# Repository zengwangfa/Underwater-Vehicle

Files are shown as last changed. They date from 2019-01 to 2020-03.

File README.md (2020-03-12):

# ROV/AUV航行器控制中心

<p align="center">
  <a href="https://zengwangfa.top/">个人主页🕺|</a>
  <a href="./software/README.md">软件说明💻|</a>
  <a href="./hardware/README.md">硬件说明📚|</a>
  <a href="./graphic_model/README.md">机械说明🎮</a>
</p>

---

<p align="center">
  
  
  
  
</p>

## 1、简介

| 硬件 | 主控制器(STM32) | 视频与数据服务器(树莓派3B+) | 
| :--: | :--: | :--: |
|芯片型号| [STM32F407ZGT6](/docs/DataSheet/STM32F407ZGT6.pdf) | [BCM2837B0](/docs/DataSheet/BCM2835-ARM-Peripherals.pdf) |
|CPU| 32位 Cortex-M4(ARMv7) | 64位 Cortex-A53(ARMv8) |
|主频| 168MHz | 1.4GHz |
|RAM| 192KB | 1GB |
|外存| 1MB(FLASH) | 32GB(SD) |
|单元| FPU、DSP | 千兆以太网 |
|操作系统| [RT-Thread](https://www.rt-thread.org/) | [Liunx](https://www.linux.org/) |
- 系统结构简图：
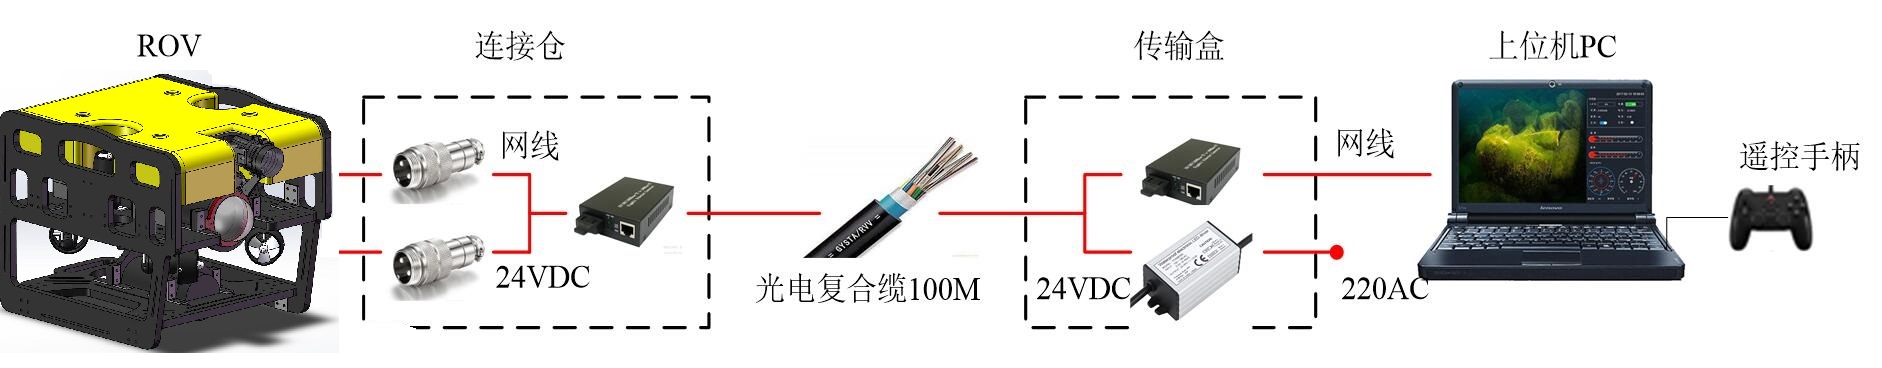
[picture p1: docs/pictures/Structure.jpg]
系统结构简图


## 2、目录说明
```
+——Underwater_vehicle
|---- docs: 【设计文档】
|---- hardware:【电路设计】      
|---+ software:【软件设计】
|       ├──README.md
|       ├──rt-thread-master
|            └──bsp
|               └──stm32f407【控制程序】
|---- graphic_model:【机械模型】
|---- raspberry_server:【树莓派服务】
|---- tools:【调试工具】
|---- README.md
```

## 3、机械结构
- 3维模型
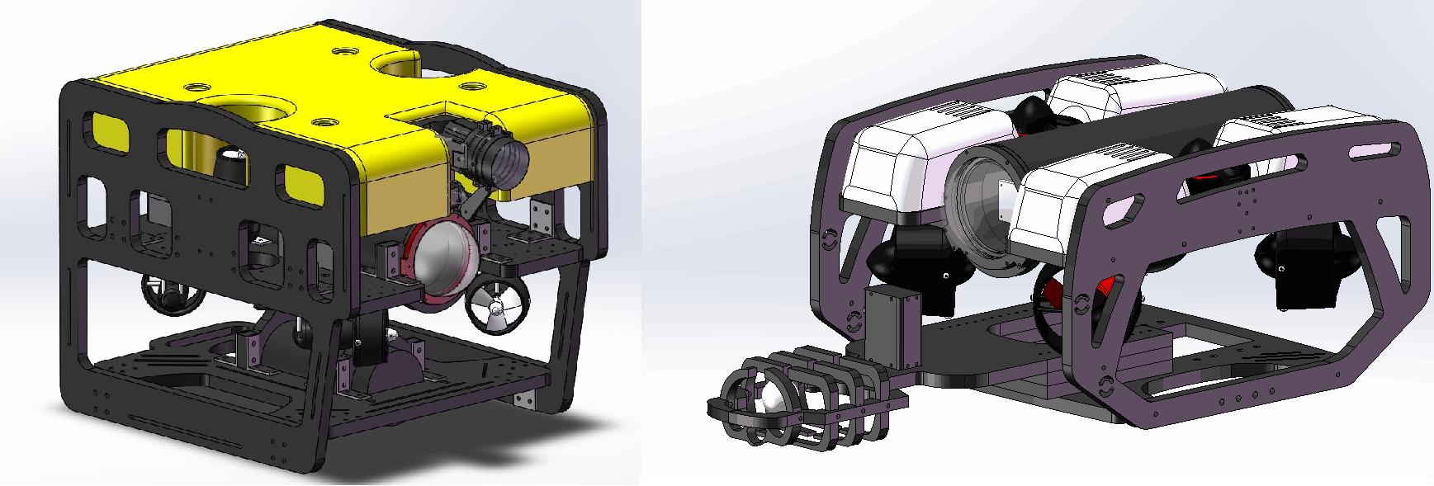
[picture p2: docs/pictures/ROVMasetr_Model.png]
ROV 3D ROVMaser Model


- 实物图
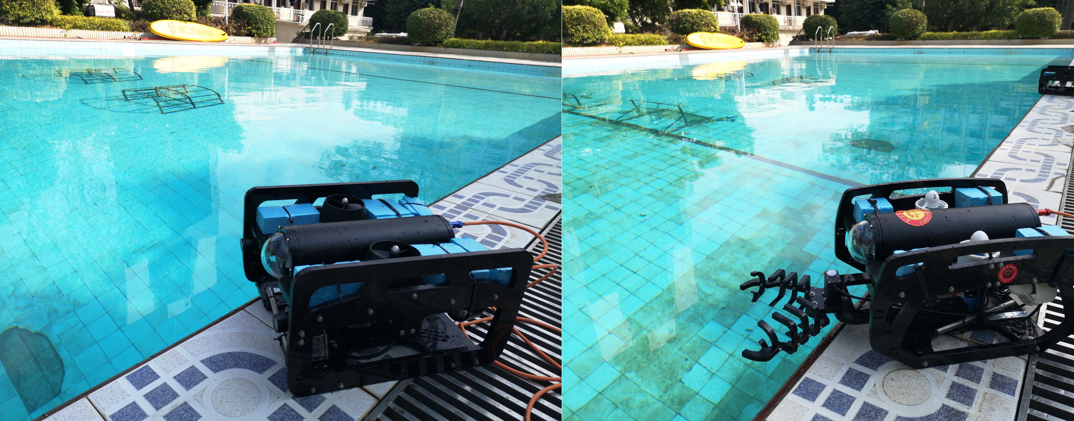
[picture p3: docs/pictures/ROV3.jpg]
Entity ROV Entity


## 4、软件结构
Connect Flow

- Computer Connect
- Raspberry Pi    
- MCU Controller  

## 5、硬件结构
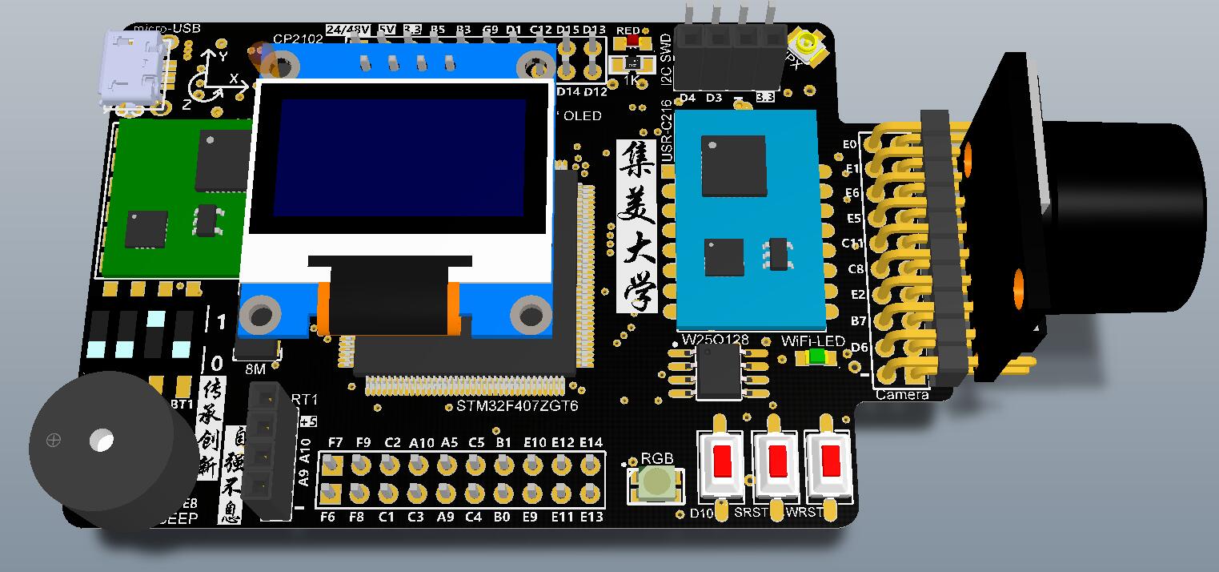
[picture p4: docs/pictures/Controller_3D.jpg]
Controller PCB 3D Controller 3D


- 核心板(Core Controller)拥有外设：

| 外设名称 | RGB LED | Key | Buzzer | Dial Switch | MS5837 | OLED | W25Q128 | Voltage Detection | Current Detection | Zigbee |  JY901 | USR-C216 | CP2102 | OV2640 Camera | Servo Motor | Searchlights | Perpellers |
| :---: | :---: | :---: | :---: | :---: | :---: | :---: | :---: | :---: | :---: | :---: | :---: | :---: | :---: | :---: | :---: | :---: | :---: |
| 控制(通讯)方式 | GPIO | GPIO | GPIO | GPIO | I2C | SPI | SPI | ADC | ADC | USART | USART | USART  | USART | DCMI-DMA | PWM | PWM | PWM |
| 功能描述 | 指示灯 | 按键 | 蜂鸣器 | 拨码开关 | 深度传感器 | 显示屏 | 闪存芯片 | 电压检测 | 电流检测 | 2.4G无线通信 | 九轴 | WiFi模块 | 串口转USB | 摄像头 | 舵机  | 探照灯 | ESC |

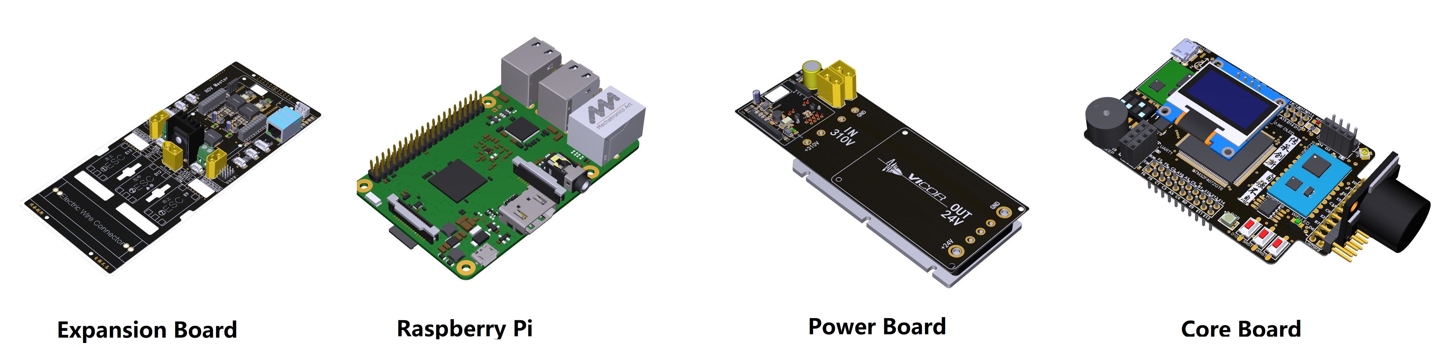
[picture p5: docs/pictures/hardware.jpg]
Hardware PCB 3D


---

- 树莓派拥有有外设：

| 外设名称 | Camera 1 | Camera 2 | Core Controller | PLC / Optical-to-electrical Transducer |
| :---: | :---: | :---: | :---: | :---: |
| 控制(通讯)方式 | USB | USB | USB | Ethernet |
| 功能描述 | 外置光学变焦摄像头 | 内置云台摄像头 | 核心控制器 | 电力载波模块/光电转换器 | 

## 6、Underwater Vehicle 的进展
- [X] 电路设计
    - [X] Core Controller核心控制板 by [@Ian](https://github.com/zengwangfa)	
	- [X] Underwater_Vehicle主板 by [@Ian](https://github.com/zengwangfa)	
	- [X] 电源主板设计 by [@Ian](https://github.com/zengwangfa)
	
- [X] 控制程序
    - [X] 外设驱动 by [@Ian](https://github.com/zengwangfa)
	- [X] 控制简易框架 by [@Ian](https://github.com/zengwangfa)
	- [X] 通信控制 by [@Ian](https://github.com/zengwangfa)
	- [X] 定向控制算法 by [@Okurarisona](https://github.com/Okurarisona) 🆕
- [X] 上位机
	- [X] C#上位机 by [@陈信任] 🆕

- [X] 机械结构
	- [X] 框架式结构CAD设计 by [@JackyLin](https://github.com/JackyLin1205) 🆕
	- [X] 电子仓、电源仓设计 by [@JackyLin](https://github.com/JackyLin1205)

- [X] 树莓派
	- [X] 数据Server服务器 by [@FatihBo](https://github.com/FatihBo)

## 7、使用说明

- propeller_power_set [parameter]
> 设置推进器动力 <0~300%>
- set_depth_sensor_type [parameter]
> 修改深度传感器 类型<ms5737/spl1301/null>
...
#### 参与贡献

- Fork 本仓库
- 新建 Feat_xxx 分支
- 提交代码
- 新建 Pull Request
- [点击联系我](Mailto:zengwangfa@outlook.com)

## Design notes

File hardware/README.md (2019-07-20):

[软件说明](./../software/README.md)|
[硬件说明](./../hardware/README.md)| 
[机械结构说明](./graphic_model/README.md)

# 1.航行器控制中心

| 硬件 | 描述 |
| -- | -- |
|芯片型号| STM32F407ZGT6 |
|CPU| Cortex-M4 |
|主频| 84MHz-168MHz |
|FLASH| 1MB |
|SRAM| 192KB |
|单元| FPU、DSP |

Controller PCB 3D Controller 3D.jpg

# 2.硬件目录
**Hardware:【相关硬件设计】**

| 目录组 | 描述 |
| --- | --- |
| Core Controller | ROV核心控制板PCB文件 |
| Depth Sensor | 深度传感器MS5837 V1.0 |
| Robot Main Board | ROV主控板PCB文件及Robot设备管理文件 |
| SMT | 钢网PDF文件 |
| Zoom Camrea Controller | 变焦摄像头PCB文件 |
# 3.硬件架构

- 拥有外设：

| 外设名称 | RGB LED | Key | Buzzer | Dial Switch | MS5837 | OLED | W25Q128 | Voltage Detection | Current Detection | Zigbee |  JY901 | USR-C216 | CP2102 | OV2640 Camera | Servo Motor | Searchlights | Perpellers |
| --- | --- | --- | --- | --- | --- | --- | --- | --- | --- | --- | --- | --- |  --- | --- |  --- |  --- | --- |
| 控制方式 | GPIO | GPIO | GPIO | GPIO | I2C | SPI | SPI | ADC | ADC | USART | USART | USART  | USART | DCMI-DMA | PWM | PWM | PWM |
| 功能描述 | 指示灯 | 按键 | 蜂鸣器 | 拨码开关 | 深度传感器 | 显示屏 | 闪存芯片 | 电压检测 | 电流检测 | 2.4G无线通信 | 九轴 | WiFi模块 | 串口转USB | 摄像头 | 舵机  | 探照灯 | 推进器 |

- 指示灯：显示系统工作状态[绿色闪烁为正常、红色常亮为异常]
- 按键：目前为切换OLED界面
- 蜂鸣器：报警提示作用
- 拨码开关：切换状态
- 深度传感器：采集水压、水温,并转换为深度值
- OLED显示屏：显示相关数据及状态
- 闪存芯片：存储相关变量及参数
- 电压检测：检测电源电压
- 电流检测：检测总电流大小,用于过流保护
- 2.4G通信模块：用于与操作系统交互
- 九轴：采集加速度、角速度、磁场、角度[偏航角Yaw、横滚角Roll、俯仰角Pitch]
- WiFi模块：用于上位机数据示波器显示及调参
- 串口转USB：用于与**树莓派**通信
- 摄像头：STM32自带摄像头,可用于扩展
- 舵机：分为云台舵机、机械手舵机
- 探照灯：用于水下照明
- 推进器：ROV/AUV动力来源

```
+——Underwater_vehicle
|--------+──DC 24V/48V 【Power management】 
|--------+──STM32F407ZGT6 【Control-Center】                  
|        |       └──【Normal Peripherals】
|        │       ├── RGB [GPIO]   
|        │       ├── KEY [GPIO] 
|        │       ├── BUZZER [GPIO]      
|        │       ├── Dial Switch [GPIO]   
|        │       ├── OLED [Software SPI]       
|        │       ├── Voltage Detection [ADC]             
|        │       ├── Bluetooth [UART]       
|        │       ├── W25Q128 FLASH [SPI]
|        │       ├── USB to serial port CP2102 UART Bridge [UART]
|        │       └──......  
|        |       └── 【Important Peripherals】
|        |       ├── Nine axis gyroscope [UART]
|        |       ├── USR-C216 Wifi [UART]   
|        |       ├── OV2640 Camera [DCMI-DMA]
|        |       └──...... 
|        +──Vehicle Devices
|        └── Searchlights [GPIO]
|        ├── Propellers [PWM]
|        ├── Servo Motor for Mechanical Arm [PWM]
|        ├── CAMERAs 
|        └──...... 
```
输入图片说明
输入图片说明 Controller PCB.jpg
------
### 2.1 电源及 USB
核心板可以通过 Micro-USB 或 5V 电源供电。使用 Micro-USB 接到电脑时，电脑弹出串口CP210x USB to UART Bridge。连接该串口后，可以通过 shell 命令行工具进行交互，也可以查看实时的日志信息。

### 2.2 功能接口
|接口|数量|备注|
|:-:|:-:|:-:|
|GPIO|2路|其他路均可复用为GPIO|
|DAC|1路|DAC2|
|ADC|5路|ADC123|
|TIM|16路|TIM4等|
|UART|2路|UART4 —— UART5|
|SPI|1路|SPI1|
|CAN|1路|CAN1|
|OV-Camera|1路|DCMI|

### 2.3 其他接口

|接口|数量|备注|
|:-:|:-:|:-:|
|POWER IN|1路|电源电压接入口|
|Bluetooth|1路|UART4|
|SWD调试接口|1路|SWD|
|气压计|1路|I2C|
|OLED|1路| SPI|
|BOOT|1路|BOOT0|
|GND|2路|电源地接入口|
|+5V|1路|+5V电压接入口|
|+3.3V|1路|+3.3V电压接入口|

### 2.4 指示灯
- Power-LED:+3.3V电源指示灯
- RGB: User 自定义指示灯
- Wifi-LED: Wifi连接指示灯

### 2.5 按键
- WRST:Wifi RESET 恢复出厂设置按键【长按3s】
- SRST:STM32 RESET 复位
- D10:GPIO-PD10 自定义【OLED下一页】

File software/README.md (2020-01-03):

[软件说明](./../software/README.md) |
[硬件说明](./../hardware/README.md) | 
[机械结构说明](./graphic_model/README.md)



- 本项目用用到了两个实用的软件包：
	- [EasyFlash](https://github.com/armink/EasyFlash)一款开源的轻量级嵌入式Flash存储器库
	- [EasyLogger](https://github.com/armink/EasyLogger)一款超轻量级、高性能的 C/C++ 日志库

# 1.目录说明

**software:【相关软件设计】**
```c
   └──Camera 【OV2640例程】
   ├──RT-Thread 【RTT示例】
   ├──rt-thread-master
        └──bsp
            └──stm32f40x 【控制中心程序】

```			

| 目录组 | 描述 |
| -- | -- |
|Kernel| 它用于存放RT-Thread内核源文件 |
|User| 它用于存放用户应用文件 |
|Applications| 它用于存放外设应用程序 |
|Drivers|  它用于存放相关外设驱动 |
|STM32_StdPeriph| 它用于存放STM32固件库文件 |
|cpu|  它用于存放内核相关文件 |
|Fliesystem| 它用于存放虚拟文件系统 |
|DeviceDrivers|  它用于存放RT-Thread驱动 |
|finsh| 它用于存放RT-Thread Finsh组件 |
|libc| 它用于存放RT-Thread 相关文件 |
|Easylogger| 它用于存放RT-Thread Easylogger组件 |
|EasyFlash| 它用于存放RT-Thread EasyFlash |
|Utilities| 它用于存放相关工具与滤波算法 |

# 2.软件结构
```
+——RT-Thread
|    └──Kernel 【RT-Thread内核初始化】                  
|    ├── Normal Peripherals Init 【普通外设初始化】
|    ├── System self-check 【系统自检:检测是否所有外设初始化完成】 
|           └── Read Gyroscope data 【读取JY901 九轴数据】 
|           ├── Detection input devices 【检测输入设别】 
|           ├── Attitude Control 【姿态控制】 	
|    └──...... 
```

# 3.定义通信协议

## 3.1 PC端发送的控制数据包

- 全部数据按照**16进制**
- 定义机头方向为X轴,机头朝向为x正方向
- 定义垂直于机头方向为y轴,向左为y正方向

| 编号 | 1 | 2 | 3 | 4 | 5 | 6 | 7 | 8 | 9 | 10 | 11 | 12 | 13 | 14 | 15  | 16 | 17 | 18 | 19 | 20 | 
| --- | --- | --- | --- | --- | --- | --- | --- | --- | --- | --- | --- | --- | --- | --- | --- | --- | --- | --- | --- | --- |
| 数据所代表的含义 | 包头 | 包头 | 数据长度位 | 深度锁定位 | 方向锁定位 | X轴动力模拟量 | Y轴动力模拟量 | 垂直运动方向位 | 旋转运动方向位 | 油门量 | 灯亮度控制位 | 变焦摄像头动作位 | 云台控制位 | 机械臂控制位 | Reserve | Reserve | Reserve | Reserve | 启动停止位 | 校验位 |  
| 具体描述 | AA | 55 | 10 |  |  |  |  |  |  |  |  |  |  |  | x | x | x | x | ON/OFF | SUM | 
| 数组编号 | 0 | 1 | 2 | 3 | 4 | 5 | 6 | 7 | 8 | 9 | 10 | 11 | 12 | 13 | 14 | 15  | 16 | 17 | 18 | 19 | 

控制字格式：0xAA 0x55 0x10+控制字节(16字节)+校验字(所有字节相加后，保留最后一个字节)

- 第1字节：包头位
- 第2字节：包头位
- 第3字节：数据长度位
- 第4字节：0x01表示深度锁定，0x02表示人工控制（可指定默认值）
- 第5字节：0x01表示方向锁定，0x02表示随水动（可指定默认值）
- 第6字节：【左摇杆上下状态】摇杆模拟量 前后状态（0~255）即摇杆居中时为128（即停止），最下为0，最上位255 
- 第7字节：【左摇杆左右状态】摇杆模拟量 左右状态（0~255）即摇杆居中时为128（即停止），最左为0，最右为255
- 第8字节：【右摇杆上下状态】摇杆模拟量 上下状态（0~255）即摇杆居中时为128（即停止），最下为0，最上位255 
- 第9字节：【右摇杆左右状态】摇杆模拟量 旋转状态（0~255）即摇杆居中时为128（即停止止），最左为0，最右为255
- 第10字节：0x00~0xff (0~255) 表示的油门大小：4档位可调，LB加档，LT减档，可分别设置4个档位油门大小 【不用】
- 第11字节：灯的亮度控制，0x01表示变亮，0x02表示变暗，0x00表示不动作（默认）
- 第12字节：摄像头焦距控制，0x01表示聚焦，0x02表示变放焦， 0x11表示放大，0x12表示缩小，0x00表示不动作（默认）
- 第13字节：云台转动，0x01表示向上，0x02表示向下，0x03表示归中，0x00表示不动作（默认）
- 第14字节：机械手动作，0x01表示张开，0x02表示关闭，0x00表示不动作（默认）
- 第15字节：保留(reserve)
- 第16字节：保留(reserve)
- 第17字节：保留(reserve)
- 第18字节：保留(reserve)
- 第19字节：0x00 默认 0x01表示启动， 0x02表示停止
- 第20字节：累加和校验

## 3.2 ROV/AUV返回的数据包

控制字格式：0xAA 0x55 0x16+控制字节(22字节) +校验字(所有字节相加后，保留最后一个字节)

- 第一，二字节：电压第一字节表示整数部分，第二字节小数部分
- 第三，四字节：舱外水温度第一字节表示整数部分，第二字节小数部分
- 第五，六字节：舱内CPU内核温度第一字节表示整数部分，第二字节小数部分
- 第七字节：深度值（0~16777215cm）精确到厘米 【高8位】
- 第八字节：深度值（0~16777215cm）精确到厘米 【中8位】
- 第九字节：深度值（0~16777215cm）精确到厘米 【低8位】
##### 深度值共由3个字节，24位组成
- 第十字节：航向角（Yaw）  【高8位】记为YawH
- 第十一字节：航向角（Yaw）【低8位】记为YawL
计算方法：偏航角（z 轴）Yaw=((YawH<<8)|YawL)/32768*180(°)
航向角（Yaw），两字节(0~359)可用0度代表正北方，90度代表正东，以此类推

- 第十二字节：俯仰角（Pitch）【高8位】记为PitchH
- 第十三字节：俯仰角（Pitch）【低8位】记为PitchL
计算方法：俯仰角（y 轴）Pitch =((PitchH<<8)| PitchL)/32768*180(°)
俯仰角（Pitch），可用0°表示水平

- 第十四字节：横滚角（Roll）【高8位】记为RollH
- 第十五字节：横滚角（Roll）【低8位】记为RollL
计算方法：横滚角（x 轴）Roll =((RollH<<8)| RollL)/32768*180(°)
横滚角（Roll），可用0°表示水平

- 第十六字节：航行速度（0~255）单位m/s

- 第17字节：设备状态标志，0x00表示都正常操作，0x01表示机械手开到头了，0x02表示摄像头转到头了，0x03表示机械手和摄像头都转到头了

| 设备状态标志8bit | 1 | 1 | 1 | 1 | 1 | 1 | 1 | 1 |
| :---: | :---: |  :---: |  :---: | :---: |  :---: | :---: | :---: | :---: |
| 代表含义 |深度传感器初始化成功  | 所有串口设备初始化成功 | IO设备初始化成功 |PWM设备初始化成功  | 聚焦开到头 | 变焦开到头 | 云台开到头 |机械手到头  |

- 第18字节：本设备的启动停止位（若返回的为0x01，代表本设备为启动状态；若为0x02 或 0x00，代表本设备为停止状态；则上位机 【P】图标需要对应）
- 第19字节：保留
- 第20字节：保留
- 第21字节：保留
- 第22字节：保留

所以，我们发送的字符串就应该为：
0xAA 0x55 0x10 控制字节(16字节) 校验字(所有字节相加后，保留最后一个字节)
若需其他的数据发送，按照此数据格式自行添加即可

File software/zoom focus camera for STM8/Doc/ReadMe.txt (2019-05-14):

一、工程说明
    1、时间：    2017年06月29日
    2、开发环境：IAR for STM8 V2.20
    3、标准库：  V2.2.0
    4、工程版本：V1.0.0
    5、目标芯片：STM8S/AF系列芯片

二、提示：
    本工程适合STM8S和STM8AF系列芯片，包含：
    STM8S208、STM8S207、STM8S007、STM8AF52Ax、STM8AF62Ax、STM8S105、
    STM8S005、STM8AF626x、STM8AF622x、STM8S103、STM8S003、STM8S903

    只要没有特别说明，工程都适合以上芯片，只需要修改配置为对应芯片即可。
    修改两个地方：
    1.Device芯片型号：Project -> Options -> General Options -> Target -> Device
    2.芯片型号预定义：Project -> Options -> C/C++ Compiler -> Preprocessor -> Defined Symbols

三、帮助
    微信搜索公众号：EmbeddDeveloper, 关注, 查看更多精彩内容。

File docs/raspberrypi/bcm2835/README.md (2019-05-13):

# BCM2835

The Broadcom chip used in the Raspberry Pi Model A, B, B+, Compute Module and Raspberry Pi Zero

Please refer to:

- [Peripheral specification](BCM2835-ARM-Peripherals.pdf)
- [GPU documentation and open source driver](http://www.broadcom.com/support/)
- [ARM1176 Processor](http://www.arm.com/products/processors/classic/arm11/arm1176.php)
- [ARM1176JZF-S](http://infocenter.arm.com/help/index.jsp?topic=/com.arm.doc.ddi0301h/index.html)

Also see the Raspberry Pi 2's chip [BCM2836](../bcm2836/README.md)

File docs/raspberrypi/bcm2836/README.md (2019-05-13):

# BCM2836

The Broadcom chip used in the Raspberry Pi 2 Model B

The underlying architecture in BCM2836 is identical to BCM2835. The only significant difference is the removal of the ARM1176JZF-S processor and replacement with a quad-core Cortex-A7 cluster.

Please refer to:

- [BCM2836 ARM-local peripherals](QA7_rev3.4.pdf)
- [Cortex-A7 MPcore Processor Reference Manual](http://infocenter.arm.com/help/index.jsp?topic=/com.arm.doc.ddi0464f/index.html)

Also see the Raspberry Pi 1's chip [BCM2835](../bcm2835/README.md)

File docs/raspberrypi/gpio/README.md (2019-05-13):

# GPIO

General Purpose Input/Output pins on the Raspberry Pi

## Overview

This page expands on the technical features of the GPIO pins available on BCM2835 in general. For usage examples, see the [GPIO Usage](../../../usage/gpio/README.md) section. When reading this page, reference should be made to the BCM2835 ARM Peripherals [Datasheet](../bcm2835/README.md), section 6.

GPIO pins can be configured as either general-purpose input, general-purpose output or as one of up to 6 special alternate settings, the functions of which are pin-dependant.

There are 3 GPIO banks on BCM2835.

Each of the 3 banks has its own VDD input pin. On Raspberry Pi, all GPIO banks are supplied from 3.3V. **Connection of a GPIO to a voltage higher than 3.3V will likely destroy the GPIO block within the SoC.**

A selection of pins from Bank 0 is available on the P1 header on Raspberry Pi.

## GPIO Pads

The GPIO connections on the BCM2835 package are sometimes referred to in the peripherals datasheet as "pads" - a semiconductor design term meaning "chip connection to outside world".

The pads are configurable CMOS push-pull output drivers/input buffers. Register-based control settings are available for

- Internal pull-up / pull-down enable/disable
- Output [drive strength](http://www.scribd.com/doc/101830961/GPIO-Pads-Control2)
- Input Schmitt-trigger filtering

### Power-On States

All GPIOs revert to general-purpose inputs on power-on reset. The default pull states are also applied, which are detailed in the alternate function table in the ARM peripherals datasheet. Most GPIOs have a default pull applied.

## Interrupts

Each GPIO pin, when configured as a general-purpose input, can be configured as an interrupt source to the ARM. Several interrupt generation sources are configurable:

- Level-sensitive (high/low)
- Rising/falling edge
- Asynchronous rising/falling edge

Level interrupts maintain the interrupt status until the level has been cleared by system software (e.g. by servicing the attached peripheral generating the interrupt).

The normal rising/falling edge detection has a small amount of synchronisation built into the detection. At the system clock frequency, the pin is sampled with the criteria for generation of an interrupt being a stable transition within a 3-cycle window, i.e. a record of "1 0 0" or "0 1 1". Asynchronous detection bypasses this synchronisation to enable the detection of very narrow events.

## Alternative Functions

Almost all of the GPIO pins have alternative functions. Peripheral blocks internal to BCM2835 can be selected to appear on one or more of a set of GPIO pins, for example the I2C busses can be configured to at least 3 separate locations. Pad control, such as drive strength or Schmitt filtering, still applies when the pin is configured as an alternate function.

For more detailed information see the [Low level peripherals](http://elinux.org/RPi_Low-level_peripherals) page on the elinux wiki

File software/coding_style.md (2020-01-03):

# RT-Thread 编程风格

这是一份 RT-Thread 开发人员的开发指引。RT-Thread 做为一份开源软件，它需要由不同
的人采用合作的方式完成，这份文档是开发人员的一个指引。RT-Thread 的开发人员请遵
守这样的编程风格。同时对于使用 RT-Thread 的用户，也可通过这份文档了解 RT-Thread
代码内部一些约定从而比较容易的把握到 RT-Thread 的实现方式。

## 1.目录名称

目录名称如果无特殊的需求，请使用全小写的形式；目录名称应能够反应部分的意思，例
如各芯片移植由其芯片名称构成或芯片类别构成；components 目录下能够反映组件的意义。

## 2.文件名称

文件名称如果无特殊的需求(如果是引用其他地方，可以保留相应的名称)，请使用全小写
的形式。另外为了避免文件名重名的问题，一些地方请尽量不要使用通用化、使用频率高
的名称。

## 3.头文件定义

C语言头文件为了避免多次重复包含，需要定义一个符号。这个符号的定义形式请采用如下
的风格：

```c
    #ifndef __FILE_H__
    #define __FILE_H__
    /* header file content */
    #endif
```

即定义的符号两侧采用 "__" 以避免重名，另外也可以根据文件名中是否包含多个词语而
采用 "_" 连接起来。

## 4.文件头注释

在每个源文件文件头上，应该包括相应的版权信息，Change Log 记录：

```c
    /*
     * File      : rtthread.h
     * This file is part of RT-Thread RTOS
     * COPYRIGHT (C) 2006 - 2012, RT-Thread Development Team
     *
     *  This program is free software; you can redistribute it and/or modify
     *  it under the terms of the GNU General Public License as published by
     *  the Free Software Foundation; either version 2 of the License, or
     *  (at your option) any later version.
     *
     *  This program is distributed in the hope that it will be useful,
     *  but WITHOUT ANY WARRANTY; without even the implied warranty of
     *  MERCHANTABILITY or FITNESS FOR A PARTICULAR PURPOSE.  See the
     *  GNU General Public License for more details.
     *
     *  You should have received a copy of the GNU General Public License along
     *  with this program; if not, write to the Free Software Foundation, Inc.,
     *  51 Franklin Street, Fifth Floor, Boston, MA 02110-1301 USA.
     *
     * Change Logs:
     * Date           Author       Notes
     * 2006-03-18     Bernard      the first version
     * 2006-04-26     Bernard      add semaphore APIs
     * ...
     */
```

例如采用如上的形式。

## 5.结构体定义

结构体名称请使用小写英文名的形式，单词与单词之间采用 "_" 连接，例如：

```c
    struct rt_list_node
    {
        struct rt_list_node *next;
        struct rt_list_node *prev;
    };
```

其中，"{"，"}" 独立占用一行，后面的成员定义使用缩进的方式定义。

结构体等的类型定义请以结构体名称加上 "_t" 的形式作为名称，例如：

```c
    typedef struct rt_list_node rt_list_t;
```

因为内核中对象引用方便的缘故，采用了对象内核指针作为类型定义的形式，例如：

```c
    typedef struct rt_timer* rt_timer_t;
```

## 6.宏定义

在RT-Thread中，请使用大写英文名称作为宏定义，单词之间使用 "_" 连接，例如：

```c
    #define RT_TRUE                         1
```

## 7.函数名称、声明

函数名称请使用小写英文的形式，单词之间使用 "_" 连接。提供给上层应用使用的 API
接口，必须在相应的头文件中声明；如果函数入口参数是空，必须使用 void 作为入口参
数，例如：

```c
    rt_thread_t rt_thread_self(void);
```

## 8.注释编写

请使用英文做为注释，使用中文注释将意味着在编写代码时需要来回不停的切换中英文输
入法从而打断编写代码的思路。并且使用英文注释也能够比较好的与中国以外的技术者进
行交流。

源代码的注释不应该过多，更多的说明应该是代码做了什么，仅当个别关键点才需要一些
相应提示性的注释以解释一段复杂的算法它是如何工作的。对语句的注释只能写在它的上
方或右方，其他位置都是非法的。

## 9.缩进及分行

缩进请采用 4 个空格的方式。如果没有什么特殊意义，请在 "{" 后进行分行，并在下一
行都采用缩进的方式，例如：

```c
    if (condition)
    {
        /* others */
    }
```

唯一的例外是 swtich 语句，switch-case 语句采用 case 语句与 swtich 对齐的方式，
例如：

```c
    switch (value)
    {
    case value1:
        break;
    }
```

case 语句与前面的 switch 语句对齐，后续的语句则采用缩进的方式。

分行上，如果没有什么特殊考虑，请**不要在代码中连续使用两个以上的空行**。

## 10.大括号与空格

从代码阅读角度，建议每个大括号单独占用一行，而不是跟在语句的后面，例如：

```c
    if (condition)
    {
        /* others */
    }
```

匹配的大括号单独占用一行，代码阅读起来就会有相应的层次而不会容易出现混淆的情况。

空格建议在非函数方式的括号调用前留一个空格以和前面的进行区分，例如：

```c
    if (x <= y)
    {
        /* others */
    }

    for (index = 0; index < MAX_NUMBER; index ++)
    {
        /* others */
    }
```

建议在括号前留出一个空格(涉及的包括 if、for、while、swtich 语句)，而运算表达式
中，运算符与字符串间留一个空格。另外，不要在括号的表达式两侧留空格，例如：

```c
    if ( x <= y )
    {
        /* other */
    }
```

这样括号内两侧的空格是不允许的。

## 11.trace、log信息

在 RT-Thread 中，普遍使用的 log 方式是 rt_kprintf。rt_kprintf 在 RT-Thread 被实
现成一个采用轮询、非中断方式的字串输出，能够适合于在中断这类"即时"显示日志的场
合。因为这种轮询方式的存在，也必然会影响到日志输出的时序关系。

建议在代码中不要频繁的使用 rt_kprintf 作为日志输出，除非你真正的明白，你的代码
运行占用的时间多一些也没什么关系。

日志输出应该被设计成正常情况下是关闭状态(例如通过一个变量或宏就能够开启)，并且
当真正输出日志时，日志是易懂易定位问题的方式。"天书式"的日志系统是糟糕的，不合
理的。

## 12.函数

在内核编程中，函数应该尽量精简，仅完成相对独立的简单功能。函数的实现不应该太长
，函数实现太长，应该反思能够如何修改(或拆分)使得函数更为精简、易懂。

## 13.对象

RT-Thread 内核采用了 C 语言对象化技术，命名表现形式是：对象名结构体表示类定义、
对象名 + 动词短语形式表示类方法，例如：

```c
    struct rt_timer
    {
        struct rt_object parent;
        /* other fields */
    };
    typedef struct rt_timer* rt_timer_t;
```

结构体定义 rt_timer 代表了 timer 对象的类定义；

```c
    rt_timer_t rt_timer_create(const char* name,
        void (*timeout)(void* parameter), void* parameter,
        rt_tick_t time, rt_uint8_t flag);
    rt_err_t rt_timer_delete(rt_timer_t timer);
    rt_err_t rt_timer_start(rt_timer_t timer);
    rt_err_t rt_timer_stop(rt_timer_t timer);
```

rt_timer + 动词短语的形式表示能够应用于 timer 对象的方法。

在创建一个新的对象时，应该思考好，对象的内存操作处理：是否允许一个静态对象存在
，或仅仅支持从堆中动态分配的对象。

## 14. 用 astyle 自动格式化代码

    参数：--style=allman
          --indent=spaces=4
          --indent-preproc-block
          --pad-oper
          --pad-header
          --unpad-paren
          --suffix=none
          --align-pointer=name
          --lineend=linux
          --convert-tabs
          --verbose

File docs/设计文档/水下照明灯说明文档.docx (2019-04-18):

水下照明灯说明文档

电源输入：7-14V

灯珠参数：功率18W 6V 光通量2500流明。

控制方式：断电再上电变换档位。高亮--低亮--闪烁三档循环。

尺寸大小：外径31MM 长度53MM如图示

注意事项：严禁在空气中点亮超过30S，否则极易烧坏灯珠。

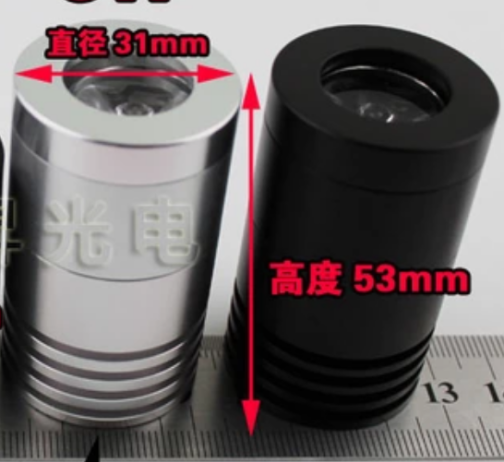
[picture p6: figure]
超级截屏_20190330_211426

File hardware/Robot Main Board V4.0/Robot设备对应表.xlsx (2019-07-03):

编号 | ① | ② | ③ | ④ | 预留接口 | 预留接口
设备 | 左下 | 左中 | 左上 | 机械臂 | 变焦摄像头 | SPI
PWM | E11 | D12 | E13 | D14 | USB接口 | I2C
 |  |  |  |  | 4路PWM | UART
编号 | ⑤ | ⑥ | ⑦ | ⑧
设备 | 右下 | 右中 | 右上 | 云台
PWM | E14 | D13 | E9 | D15

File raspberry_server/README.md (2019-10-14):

- server.py 
    - 为以树莓派作为服务器，树莓派实现接收上位机的控制数据包通过USB转发给STM32
    - 并将STM32采集到的数据【CPU温度、水深、水温、航向角、俯仰角、横滚角、航速、提示字符等】回传给上位机
- rc.local 
	- 以自启动服务方式开启python服务端（用于收发指令、传递数据）
	- 以自启动服务方式开启MJPG-Streamer推送视频流
	
# 1.MJPG-Streamer安装
[MJPG-Streamer安装与推流](https://blog.csdn.net/qq_39492932/article/details/84671345)

# 2.自启动方式
- 一、系统脚本式自启动(推荐)
- 二、桌面式自启动

## 2.1 系统脚本式自启动

- 1.将/etc/rc.local中的rc.local替换掉（如果需要多个摄像头，）
- 2.server.py 放 /home/pi 下

- 3.shell输入：
`
sudo chmod +x /etc/rc.local
`
使脚本生效（可执行）

---
- 当发现rc.local中的服务**并未自启动**，输入命令： `sudo systemctl status rc-local` 可以检查服务状态（正常状态如下图），如未启动可根据提示的**报错信息**进行相应的修改

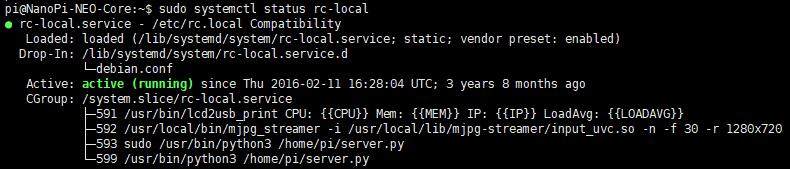
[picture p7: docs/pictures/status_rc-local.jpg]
rc.local服务状态


## 2.2 桌面式启动器	
- 1.server.py 放 /home/pi 下
- 2.autostart文件夹为 放置在树莓派 /home/pi/.config 文件夹下 **实现开机自启动**【树莓派服务器】以及【MJPG视频推流】
	- Server.desktop :【树莓派服务器】
    - MJPG0.desktop :【MJPG视频0推流】
	- MJPG1.desktop :【MJPG视频1推流】
> 只有当桌面打开,该服务程序才会打开

## 3.延迟测试
- 硬件平台：树莓派3B+（粗略测试）

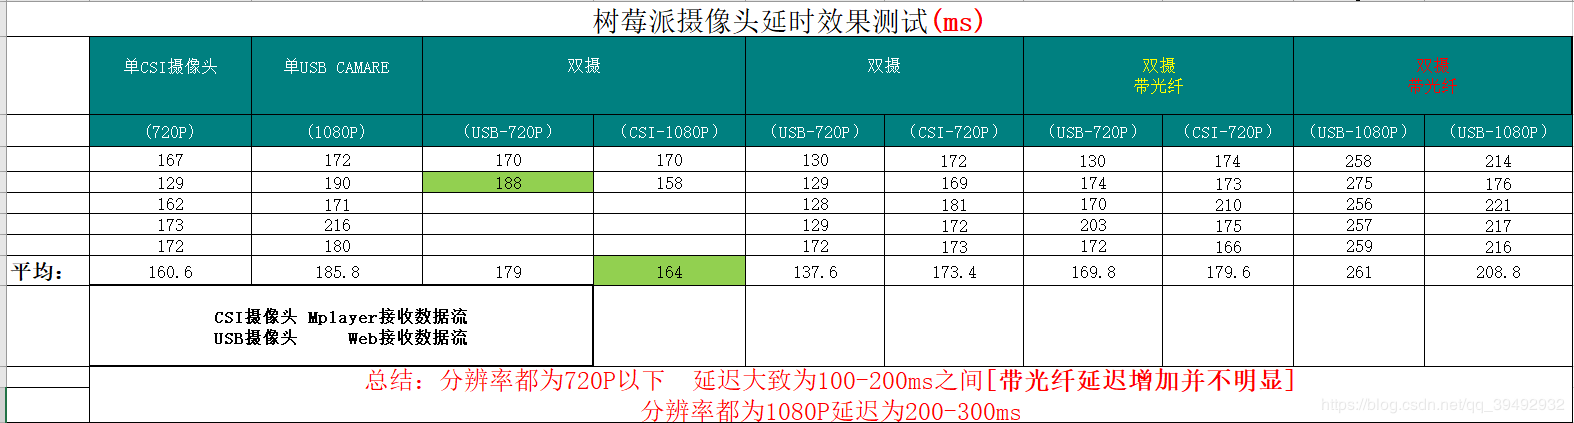
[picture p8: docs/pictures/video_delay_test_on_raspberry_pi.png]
video_delay_test_on_raspberry_pi 树莓派推流延迟测试


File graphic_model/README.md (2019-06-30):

## 1、ROV/AUV航行器控制中心

[软件说明](./../software/README.md)|
[硬件说明](./../hardware/README.md)| 
[机械结构说明](./graphic_model/README.md)

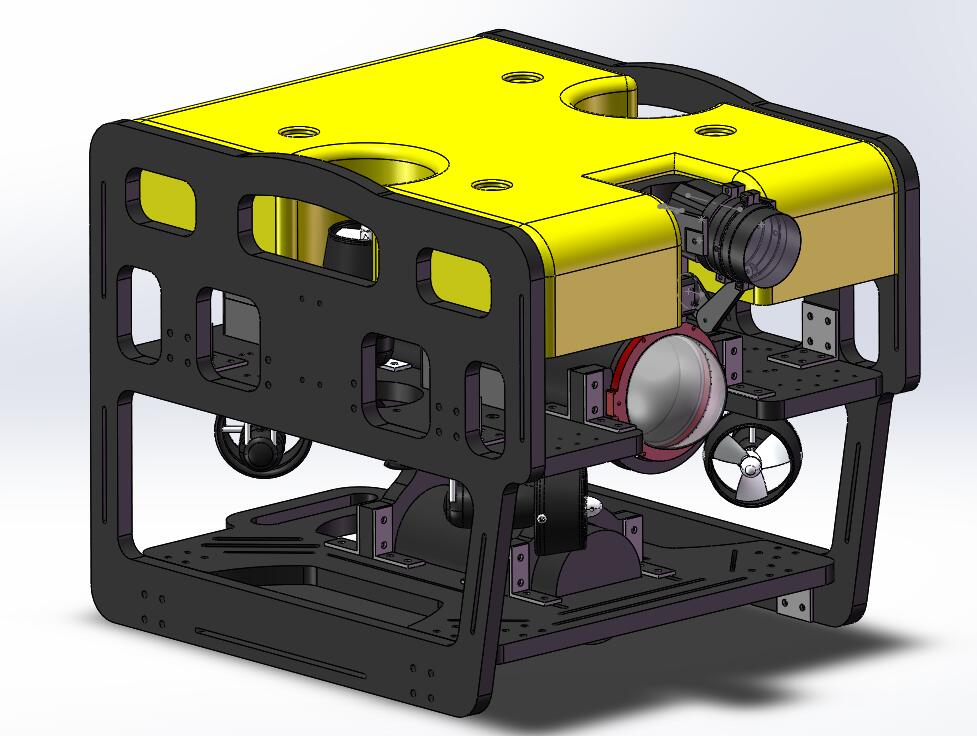
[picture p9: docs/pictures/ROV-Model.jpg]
ROV 3D


## 5、Underwater Vehicle 的进展
- [X] 电路设计
	- [X] Underwater_Vehicle核心控制板 by [@zengwangfa](https://github.com/zengwangfa)	
	- [X] Underwater_Vehicle底板 by [@zengwangfa](https://github.com/zengwangfa)	
	- [X] 变焦摄像头驱动控制板 by [@张静]	
	- [X] 电源主板设计 by [@李浩辰]	🆕
	
- [X] 控制程序
    - [X] 外设驱动 by [@zengwangfa](https://github.com/zengwangfa)
    - [X] 内置MSH方法 by [@zengwangfa](https://github.com/zengwangfa)
    - [X] debug上位机:(Vcan【山外】/Ano【匿名】) by [@zengwangfa](https://github.com/zengwangfa)
	- [X] 控制简易框架 by [@zengwangfa](https://github.com/zengwangfa)
	- [X] 通信控制 by [@zengwangfa](https://github.com/zengwangfa)🆕

- [X] 上位机
	- [X] C#上位机界面 by [@陈信任] 🆕
	- [X] 遥控器通信控制 by [@陈信任]	
	
- [X] 机械结构
	- [X] 框架式结构CAD设计 by [@林麟亮] 🆕
	- [X] 电子仓、电源仓设计 by [@林麟亮]
	- [X] 云台3D打印模型 by [@洪华霖]

- [X] 树莓派
	- [X] Server服务器by [@FatihBo](https://github.com/FatihBo)🆕

#### 使用说明

- 暂无添加

#### 参与贡献

- Fork 本仓库
- 新建 Feat_xxx 分支
- 提交代码
- 新建 Pull Request

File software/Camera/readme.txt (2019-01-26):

实验器材:
	探索者STM32F4开发板
	
实验目的:
	学习STM32F4的DCMI接口和OV2640摄像头模块的使用.
	
硬件资源:
	1,DS0(连接在PF9)
	2,串口1(波特率:115200,PA9/PA10连接在板载USB转串口芯片CH340上面)
	3,ALIENTEK 2.8/3.5/4.3/7寸TFTLCD模块(通过FSMC驱动,FSMC_NE4接LCD片选/A6接RS)
	4,按键KEY0(PE4)/KEY1(PE3) 
	5,DCMI接口(用于驱动OV2640摄像头模块)
	6,定时器3(用于打印摄像头帧率等信息)
	7,ALIENTEK OV2640摄像头模块,连接关系为:  
		OV2640模块 ------------ STM32开发板
		 OV_D0~D7  ------------  PE6/PE5/PB6/PC11/PC9/PC8/PC7/PC6
		 OV_SCL    ------------  PD6
		 OV_SDA    ------------  PD7
		 OV_VSYNC  ------------  PB7
		 OV_HREF   ------------  PA4
		 OV_RESET  ------------  PG15
		 OV_PCLK   ------------  PA6
		 OV_PWDN   ------------  PG9 

实验现象:
	本实验开机后，初始化摄像头模块（OV2640），如果初始化成功，则提示选择模式：RGB565模式，或者
	JPEG模式。KEY0用于选择RGB565模式，KEY1用于选择JPEG模式。
	
    当使用RGB565时，输出图像（固定为：UXGA）将经过缩放处理（完全由OV2640的DSP控制），显示在LCD
	上面。我们可以通过KEY_UP按键选择：1:1显示，即不缩放，图片不变形，但是显示区域小（液晶分辨率
	大小），或者缩放显示，即将1600*1200的图像压缩到液晶分辨率尺寸显示，图片变形，但是显示了整个
	图片内容。通过KE0Y按键，可以设置对比度；KEY1按键，可以设置饱和度；KEY2按键，可以设置特效。

    当使用JPEG模式时，图像可以设置任意尺寸（QQVGA~UXGA），采集到的JPEG数据将先存放到STM32F4的内
	存里面，每当采集到一帧数据，就会关闭DMA传输，然后将采集到的数据发送到串口2（此时可以通过上位
	机软件（串口摄像头.exe）接收，并显示图片），之后再重新启动DMA传输。我们可以通过KEY_UP设置输
	出图片的尺寸（QQVGA~UXGA）。通过KEY0按键，可以设置对比度；KEY1按键，可以设置饱和度；KEY2按
	键，可以设置特效。
    
    同时时可以通过串口1，借助USMART设置/读取OV2640的寄存器，方便大家调试。DS0指示程序运行状态，
	DS1用于指示帧中断。
   
注意事项: 
	1,4.3寸和7寸屏需要比较大电流,USB供电可能不足,请用外部电源适配器(推荐外接12V 1A电源).
	2,本例程在LCD_Init函数里面(在ILI93xx.c),用到了printf,如果不初始化串口1,将导致液晶无法显示!!  
	3,本实验需要自备ALIENTEK OV2640摄像头模块一个.

					正点原子@ALIENTEK
					2014-10-25
					广州市星翼电子科技有限公司
					电话：020-38271790
					传真：020-36773971
					购买：http://shop62103354.taobao.com
					http://shop62057469.taobao.com
					公司网站：www.alientek.com
					技术论坛：www.openedv.com

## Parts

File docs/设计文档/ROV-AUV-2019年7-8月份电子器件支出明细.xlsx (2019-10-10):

ROV 电子器件支出明细表
器材名称 | 数量 | 价格（元） | 日期 | 截图
双排母，单排母排母座 | 22 | 15 | 2019.07.08
A2212 A2208香蕉头 | 80 | 48 | 2019.07.09
自锁环形灯+插座 | 1 | 22.5 | 2019.07.09
XT60公母头T插 | 6 | 35.2 | 2019.07.09
肖特基二极管TO247 | 5 | 24 | 2019.07.10
邮费补差价 | 1 | 10 | 2019.07.11
1.25mm连接线双头端子线 | 30 | 27.2 | 2019.07.11
HR911105A RJ45插座，卧贴4p6p，立贴4p | 若干 | 49.6 | 2019.07.11
接线端子连接片 | 20 | 28 | 2019.07.12
贴片拨码开关，小型有源蜂鸣器5v，STM32F4077GT6 | 若干 | 131 | 2019.07.12
PCB打样 | 7 | 223 | 2019.07.13
3A可调降压模块 | 5 | 17.19 | 2019.07.13
兼容J-Link下载器 | 3 | 53.9 | 2019.07.19
XH2.54mm端子线 | 40 | 18.3 | 2019.07,19
超五类网线 | 6 | 47.31 | 2019.07.19
FLASH存储器芯片，MicroUSB插座，Micro5P插座，贴片功率电感，贴片拨码开关，贴片天线座子，STM32F407ZGT6，桥接控制器 | 若干 | 144 | 2019.07.20
舵机 | 2 | 54.7 | 2019.07.22
STM钢网制作 | 1 | 49 | 2019.07.22
PCB钢网 | 1 | 6 | 2019.07.22
接线端子连接片 | 20 | 28 | 2019.07.23
功放仪器线路板盒外壳 | 1 | 29.8 | 2019.07.25
双头端子线 | 30 | 28.3 | 2019.07.25
功放仪器线路板盒外壳 | 2 | 30 | 2019.07.25
大功率二极管30A | 1 | 21.8 | 2019.08.02
捷配PCB打样 | 9 | 285 | 2019.08.02
捷配PCB打样 | 10 | 50 | 2019.08.02
STM钢网 | 1 | 39 | 2019.08.04
 | 合计 | 1515.8

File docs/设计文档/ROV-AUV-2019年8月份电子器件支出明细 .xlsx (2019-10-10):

ROV 电子器件支出明细表
器材名称 | 数量 | 价格（元） | 日期 | 截图
SMBJ3.3A 单向TVS瞬变抑制二极 (https://item.taobao.com/item.htm?id=554187140720&_u=11v2ldgs53e4) | 20 | 11 | 2019.8.6
wifi低功耗模块贴片式串口转 (https://item.taobao.com/item.htm?id=554833317021&_u=11v2ldgscbb1) | 5 | 153 | 2019.8.6
STM32、CP2102 | 10 | 204.7 | 2019.8.6
1.25mm连接线 (https://item.taobao.com/item.htm?id=577131806740&_u=11v2ldgsa004) | 20 | 22.2 | 2019.8.17
香蕉头3.5mm 公母 | 100 | 83 | 2019.8.21
16MM金属自锁启动停 (https://item.taobao.com/item.htm?id=587873748770&_u=11v2ldgs3e2e) | 4 | 74.4 | 2019.8.21
1.25mm连接线 (https://item.taobao.com/item.htm?id=577131806740&_u=11v2ldgsa004) | 20 | 22.2 | 2019.8.21
排针排母连接器、采样电阻、STM32 | 若干 | 71.2 | 2019.8.21
TB-1508接线端子接线排连接器15A (https://item.taobao.com/item.htm?id=591125397884&_u=11v2ldgs4149) | 10 | 21 | 2019.8.21
88X38仪表铝型材壳体 (https://item.taobao.com/item.htm?id=546070757550&_u=11v2ldgs5598) | 2 | 58.6 | 2019.8.22
15pF 8MHZ贴片晶振 (https://item.taobao.com/item.htm?id=573436370330&_u=11v2ldgs96ea) | 20 | 18.6 | 2019.8.22
电饭锅电源插座 品字形插座 (https://item.taobao.com/item.htm?id=540806842796&_u=11v2ldgse690) | 10 | 29.2 | 2019.8.24
共计 |  | 769.1
 | 合计 | 1538.2

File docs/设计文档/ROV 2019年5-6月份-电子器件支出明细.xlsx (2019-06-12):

ROV 电子器件支出明细表
器材名称 | 数量 | 价格（元） | 日期 | 备注
陶瓷谐振器 8M 晶振 | 10 | 7.8 | 2019.04.15
KF129-2P/3P、瞬态抑制二极管、 保险丝、RJ45、磁珠 | 若干 | 74 | 2019.04.15
VLC6045 贴片电感 | 12 | 70.56 | 2019.04.17
USB转2.54端子 定做 | 4 | 50.02 | 2019.04.17
RT7272、RT8289 电源芯片 | 10 | 40 | 2019.04.22
XH2.54MM 2P/3P/6P 蓝白排线 | 40 | 36.93 | 2019.04.22
B550C 二极管 | 5 | 5.75 | 2019.04.22
TPS564201 电源芯片 | 5 | 45.05 | 2019.04.22
KF2EDGK 5.08mm 端子、XT60端子 、2*10排母 | 若干 | 39.88 | 2019.04.23
STM32F407ZGT6、CP2102、W25Q128、OLED12864、天线、RGB、排针排母、拨码开关、蜂鸣器 | 若干 | 118 | 2019.04.23
BLM31KN121SN1L 磁珠 | 5 | 21.5 | 2019.04.23
钽电容47uF/35V | 15 | 37.5 | 2019.04.24
TLV62568 电源芯片 | 10 | 27 | 2019.04.25
USB转micro USB 线 | 4 | 36.9 | 2019.04.29
散热片 | 6 | 14.75 | 2019.05.09
扇热风扇 | 3 | 15 | 2019.05.19
 | 总计： | 640.64

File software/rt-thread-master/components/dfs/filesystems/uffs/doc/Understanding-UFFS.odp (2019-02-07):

## Understanding UFFS

Ricky Zheng

< ricky_gz_zheng@yahoo.co.nz >

Created: March 2007

Last modified: Nov 2011

## Content

- Why UFFS ?
- Design goal
- Flash: NOR vs NAND ?
- What's wrong with FAT ?
- UFFS basic idea
  - Serial number
  - Tree in memory
  - Journalizing
- UFFS architecture
  - UFFS device
  - Mount point
  - UFFS nodes tree
  - Mounting UFFS
  - Page spare/UFFS tags
  - Block info cache
  - UFFS page buffer
  - Block recover
  - Bad block management
  - How ECC works ?
  - Flash interface
- What's next ?
  - UFFS2

## Why UFFS ?

- JFFS/JFFS2
  - Can't go out of Linux/MTD
  - Memory monster
- YAFFS/YAFFS2 still consumes too much RAM
  - 64M FLASH, 500 files ==> 410K RAM
- No open source lightweight flash file system exists yet ...

## UFFS design goal

- Ultra low cost
  - Low memory cost
  - Fast booting
- Superb Stability
  - Constant RAM consumption, support static memory allocation
  - Guaranteed integrity across unexpected power losses
  - Bad block tolerant, ECC and ware leveling
- NAND flash friendly
  - Support small (512B) or large page (up to 4KB) size
  - Support SLC and MLC
  - Support software ECC or hardware ECC / RS-ECC
  - Direct flash interface
- Well Emulated on PC platform, easy for debugging

## Flash: NOR vs NAND

- NOR:
  - Random access for read
  - Big block (minimal erase unit)
  - Byte programing
  - Slow erasing/programing
- NAND:
  - Page/spare access for read
  - Small block
  - Page/spare programing (with limited splits/Restricted rewrite)
  - Fast erasing/programing
  - Delivered with bad blocks

## NAND Flash Basic

Page data

Spare

Block

Erase: '0'->'1', Write/Program: '1'->'0'

## What's wrong with FAT

- Need FTL (which may cost many RAM)
- Big FAT table,slow down the whole system
- Vulnerable when unexpectedly interrupted while updating FAT or File info

FAT

File info

Changes

Write File

Changes

File data

Changes

## UFFS basic idea(1)

Parent

Serial

Parent

Serial

Parent

Serial

Parent

Serial

Parent

Serial

Parent

Serial

Parent

Serial

Parent

Serial

Parent

Serial

- Use unique parent/serial number pair to:
  - Identify blocks
  - Build relationships

ROOT

Parent: 16 bit

Serial: 16 bit

## UFFS basic idea(2)

- Build the relationship tree in memory when mounting UFFS:
  - Erased blocks
  - Bad blocks
  - Hash tables (serial number as key)
    - Dir table
    - File table
    - File data table
- Tree node size: 16 bytes
  - Memory cost: 16 * total_blocks

## UFFS basic idea(3)

- Journalizing
  - Write to a new block/page instead of modify the old one.
  - Use circular time stamp: 00->01->11->00>...
  - Check and correct conflicts while mounting UFFS
  - Using “mini-header” eliminates partial page programing requirement

## UFFS Device

- UFFS Device & Mount Point

extern uffs_Device uffs_rootDev;

extern uffs_Device uffs_dataDev;

static struct uffs_mountTableSt femu_MountTbl[] = {

{&uffs_rootDev, 0, 200, "/"},

{&uffs_dataDev, 201, -1, "/data/"},

{NULL, 0, 0, NULL},

};

“/”

“/data/”

UFFS Device ===> Partition
UFFS Device: individual flash ops, cache/buffer, tree nodes ...

## UFFS node tree

- UFFS nodes tree

UFFS device

Bad blocks

Erased blocks

Dir nodes

File nodes

Data nodes

Hash table, serial as the key

block,next

block,next

block,parent,serial,sum,next

block,parent,serial,sum,length(4),next

block,parent,serial,length(2),next

sizeof(TreeNode) = 16B

## UFFS Mounting

- Mounting UFFS

Step 1:

  - Scan page spares*, classify DIR/FILE/DATA nodes
  - Check bad block
  - Check interrupted writing

Step 2:

  - Randomize erased blocks

Step3:

  - Check DATA nodes,take care orphan nodes

Super fast !

* UFFS only read a few spares (normally one or two) from each block rather then all spares !!

UFFS device

Bad blocks

Erased blocks

Dir nodes

File nodes

Data nodes

## UFFS tags

- Page spare/UFFS tags

struct uffs_TagStoreSt {

u32 dirty:1;

u32 valid:1;

u32 type:2;

u32 block_ts:2;

u32 data_len:12;

u32 serial:14;

u32 parent:10;

u32 page_id:6;

u32 reserved:4;

u32 tag_ecc:12;

};

sizeof(struct uffs_TagStoreSt) = 8, small enough to store on spare area

* Note: if using RS-ECC on small page MLC, then tag may store on page data area

## UFFS block info cache

- UFFS block info cache

struct uffs_pageSpareSt {

u8 expired:1;

uffs_Tags tag;

};

struct uffs_blockInfoSt {

struct uffs_blockInfoSt *next;

struct uffs_blockInfoSt *prev;

u16 blockNum;

struct uffs_pageSpareSt *spares;

int expiredCount;

int refCount;

};

uffs_config.h:

MAX_CACHED_BLOCK_INFO(5 ~10)

Memory: 40 bytes for each cached info

## UFFS page buffer

- UFFS page buffer

struct uffs_BufSt{

struct uffs_BufSt *next;

struct uffs_BufSt *prev;

struct uffs_BufSt *nextDirty;

struct uffs_BufSt *prevDirty;

u8 type;

u8 ext_mark;

u16 parent;

u16 serial;

u16 pageID;

u16 mark;

u16 refCount;

u16 dataLen;

u8 * data;

u8 * header;

};

uffs_config.h:

MAX_PAGE_BUFFERS (10 ~ 40)

Memory: (40 + page_size) each buffer

## UFFS page status

Valid page

Discarded page

Free page

- Free page: no page id assigned yet. Free pages are always on the bottom.
- Valid page: the page with a id and have max page offset
- Discarded page: the page with page id, there are one or more pages have the same id and bigger page offset.
- Unknown status: interrupted while writing a page.

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
## UFFS block status

Valid page

Discarded page

Free page

- Bad block
- Free/Erased block
- Non-full loaded block (have one or more free pages)
- Full loaded block (no free page, page id = physical page offset)

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
Bad block

Free block

Non-full loaded block

13

14

15

Full loaded block

## UFFS block recover(1)

- Block recover happens when:
  - No more free pages available inside the block and
  - Data were modified and/or
  - Flush the buffer
- Block recover steps:
  - (1)Get a free/erased block from erased block list
  - (2)Copy pages from old block, write to new block with newer timestamps
  - (3)Erase the old block
  - (4)Put the old block to erased block list
  - Note: (1) and (4) are operating in memory. (2) and (3) identified by timestamps, all steps allow to be interrupted at any time ! (Guaranteed integrity across unexpected power losses)

## UFFS block recover(2)

- No block recover if there are enough free pages

Block 1234

0

Block 1234

0

1

1

Since there are free pages, no block recover happens.

Mark old page as discarded, and generate a new page.

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
Valid page

Discarded page

Free page

## UFFS block recover(3)

- Recover a non-full loaded block

Block 1234

0

Block 5678

0

1

No more free page available in this block, modify any pages from 0-7, or add a new page 8, will cause block recovering.

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
Valid page

Discarded page

Free page

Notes: See uffs_buf.c: static URET _BufFlush_Exist_With_BlockCover ( uffs_Device *dev, TreeNode *node, uffs_blockInfo *bc )

## UFFS block recover(4)

- Recover a full-loaded block

Block 1234

0

Block 5678

0

Modify any page of full-loaded block will cause block recovering.

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
Valid page

Discarded page

Free page

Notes: See uffs_buf.c: static URET _BufFlush_Exist_With_BlockCover ( uffs_Device *dev, TreeNode *node, uffs_blockInfo *bc )

## UFFS Page layout

Status byte

mini-

header

Seal byte

ECC

DATA

Tag

- Mini-header (4B) and DATA on page data area, Tag, ECC and 'seal byte' on spare area
- In some case (for example, when using hardware RS-ECC on small page MLC), you can treat the whole NAND page as one body, blur the page data and spare area boundary.
- The 'status byte': this is the first byte of mini-header. If status byte is not 0xFF – this page is “dirty”, page program already started.
- The 'seal byte': this is the last byte of spare data. If seal byte is not 0xFF – this page is “sealed”, all data and tag/ECC have been programmed successfully.

## UFFS bad block management

- Bad block discover when mounting UFFS
- Bad block discover when read/write/erase
  - Try ECC error correct
  - If ECC fail, there is no way get valid data
  - Do not process bad block immediately, leave it at the end of Read/Write operation.
  - Only handle one bad block during the one read/write operation.
- Check bad block when formating UFFS

## How ECC works ? (1)

- XOR: A ^ B = C
  - 0 ^ 0 = 0
  - 1 ^ 0 = 1
  - 0 ^ 1 = 1
  - 1 ^ 1 = 0
- Knowing any two of A, B and C, will know the rest one.
- UFFS ECC: 3 bytes ECC for 256 bytes data
  - 256 Bytes ==> 2048 Bits ===> 256(row) X 8(col)

## How ECC works ? (2)

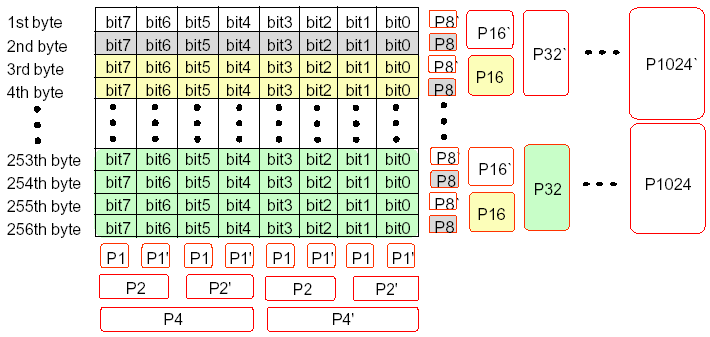
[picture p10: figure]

## UFFS Flash Interface

- struct uffs_FlashOpsSt:
  - Use hardware ECC, or leave it to UFFS
  - Allow driver do the spare layout, or leave it to UFFS
  - Return flash operation status
  - Sequential page programing. No partial page programing.

## UFFS Limitations

- Only one file/dir on one block
- Dynamic wear-leveling, Static wear-leveling is not implemented.

## The next: UFFS2 ?

- Smaller Tree Node (12 bytes), save 25% RAM
- Use NAND block as buffers
- Multiple files/dirs on one block
- Support 8K, 16K page size
- Static wear-leveling
- Symbol link, FIFO file ?
- NOR flash support ? Maybe ...

## The End

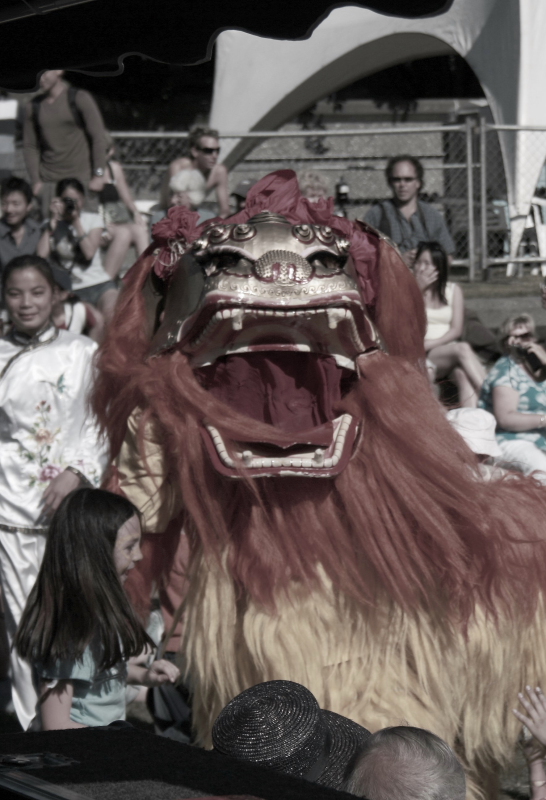
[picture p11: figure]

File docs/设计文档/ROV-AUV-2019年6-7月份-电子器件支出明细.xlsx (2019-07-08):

ROV 电子器件支出明细表
器材名称 | 数量 | 价格（元） | 日期 | 截图
BAYMAK降压芯片 | 5 | 11.4 | 2019.06.04
Risym 电解电容/高压瓷片电容器 | 若干 | 15.82 | 2019.06.05
三防漆PCB线路板防水胶 | 1 | 15.9 | 2019.06.06
AC-DC降压电源模块 | 3 | 38.4 | 2019.06.10
铝盒 线路板外壳 | 1 | 72 | 2019.06.21
22mm指示灯金属开关按钮 | 1 | 21.9 | 2019.06.22
品字形插座 | 5 | 8.6 | 2019.06.22
TO-247绝缘片散热片云母片 | 1 | 6.9 | 2019.06.22
固定式接线端子 15A | 2 | 29 | 2019.06.22
全新静音风扇 2510 2.5厘米 | 4 | 28 | 2019.06.24
散热片 | 1 | 6.7 | 2019.06.24
高速电脑网络宽带线 | 6 | 63.4 | 2019.06.29
MBR60100PT 肖特基二极管 | 2 | 12 | 2019.06.29
陶瓷谐振器 CSTCC8M00G53-R0 | 16 | 12.48 | 2019.06.30
路由器连接宽带纯铜扁网线 | 9 | 23.7 | 2019.06.30
多功能网络测试仪 | 1 | 12.9 | 2019.06.30
XT60PW 30DU 90 150香蕉插头 | 30 | 126.9 | 2019.07.01
压线钳 | 1 | 41 | 2019.07.01
10040贴片功率电感 、2512贴片合金采样电阻 、 卧贴1.25mm间距连接器 、贴片FLASH存储器芯片 、 冷压接线端子 、贴片拨码开关、 单头电子线、 双头电子线 、双头杜邦 、小型有源蜂鸣器、HR911105A RJ45插座、IPX座 、2.4G内置柔性FPC软天线、彩色单/双排排针 、 1206贴片自恢复保险丝、STM32F407ZGT6、贴片28脚USB转UART 桥接控制器 | 若干 | 462.49 | 2019.07.02
TB-1508接线端子接线排连接器 | 8 | 18.6 | 2019.07.02
万能电线连接器8孔PCT-218 | 2 | 30 | 2019.07.03
XT60公母头T插 | 21 | 89.4 | 2019.07.03
TB-1508 15A 8位接线端子 | 16 | 12.16 | 2019.07.03
TB-1504 15A 4位接线端子 | 16 | 6.88 | 2019.07.03
A2212 A2208 香蕉头 | 100 | 68 | 2019.07.03
2cm/厘米轴流散热风扇USB5V | 2 | 38 | 2019.07.03
1.25端子线单头双头线束连接线 | 45 | 21.4 | 2019.07.04
wifi低功耗模块贴片式串口转 | 7 | 194 | 2019.07.04
SMT钢网制作PCB贴片 | 1 | 55 | 2019.07.04
独立单筒可拆超大容量收纳盒 | 1 | 23.88 | 2019.07.04
300MA高速CMOS LDO稳压IC 3.3V | 20 | 1.8 | 2019.07.05
 | 合计： | 1568.61

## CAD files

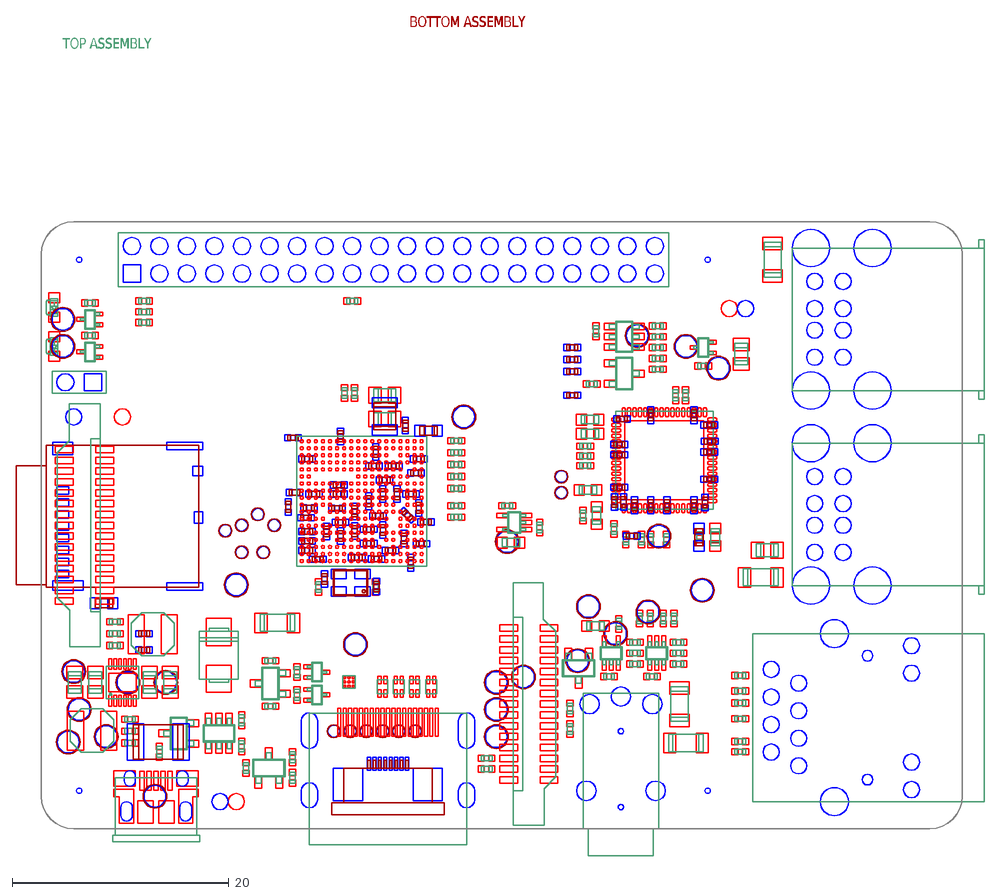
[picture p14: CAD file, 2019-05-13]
docs/raspberrypi/mechanical/Raspberry-Pi-B-Plus-V1.2-Mechanical.dxf
BOTTOM ASSEMBLY
TOP ASSEMBLY

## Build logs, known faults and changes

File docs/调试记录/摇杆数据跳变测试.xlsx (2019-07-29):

[2019/7/29 9:34:53] left: | 0 | ight: | 0
[2019/7/29 9:34:53] left: | 0 | ight: | 0
[2019/7/29 9:34:53] left: | 0 | ight: | 0
[2019/7/29 9:34:53] left: | 0 | ight: | 0
[2019/7/29 9:34:53] left: | 0 | ight: | 0
[2019/7/29 9:34:53] left: | 0 | ight: | 0
[2019/7/29 9:34:53] left: | 0 | ight: | 0
[2019/7/29 9:34:53] left: | 0 | ight: | 0
[2019/7/29 9:34:53] left: | 0 | ight: | 0
[2019/7/29 9:34:53] left: | 0 | ight: | 0
[2019/7/29 9:34:53] left: | 0 | ight: | 0
[2019/7/29 9:34:53] left: | 0 | ight: | 0
[2019/7/29 9:34:53] left: | 0 | ight: | 0
[2019/7/29 9:34:53] left: | 0 | ight: | 0
[2019/7/29 9:34:53] left: | 0 | ight: | 0
[2019/7/29 9:34:53] left: | 0 | ight: | 0
[2019/7/29 9:34:53] left: | 0 | ight: | 0
[2019/7/29 9:34:53] left: | 0 | ight: | 0
[2019/7/29 9:34:53] left: | 0 | ight: | 0
[2019/7/29 9:34:53] left: | 0 | ight: | 0
[2019/7/29 9:34:53] left: | 0 | ight: | 0
[2019/7/29 9:34:53] left: | 0 | ight: | 0
[2019/7/29 9:34:53] left: | 0 | ight: | 0
[2019/7/29 9:34:53] left: | 0 | ight: | 0
[2019/7/29 9:34:53] left: | 0 | ight: | 0
[2019/7/29 9:34:53] left: | 0 | ight: | 0
[2019/7/29 9:34:53] left: | 0 | ight: | 0
[2019/7/29 9:34:53] left: | 0 | ight: | 0
[2019/7/29 9:34:53] left: | 0 | ight: | 0
[2019/7/29 9:34:53] left: | 0 | ight: | 0
[2019/7/29 9:34:53] left: | 0 | ight: | 0
[2019/7/29 9:34:53] left: | 0 | ight: | 0
[2019/7/29 9:34:53] left: | 0 | ight: | 0
[2019/7/29 9:34:53] left: | 0 | ight: | 0
[2019/7/29 9:34:53] left: | 0 | ight: | 0
[2019/7/29 9:34:53] left: | 0 | ight: | 0
[2019/7/29 9:34:53] left: | 0 | ight: | 0
[2019/7/29 9:34:53] left: | 0 | ight: | 0
[2019/7/29 9:34:53] left: | 0 | ight: | 0
[2019/7/29 9:34:53] left: | 0 | ight: | 0
[2019/7/29 9:34:53] left: | 0 | ight: | 0
[2019/7/29 9:34:53] left: | 0 | ight: | 0
[2019/7/29 9:34:53] left: | 0 | ight: | 0
[2019/7/29 9:34:53] left: | 0 | ight: | 0
[2019/7/29 9:34:53] left: | 0 | ight: | 0
[2019/7/29 9:34:53] left: | 0 | ight: | 0
[2019/7/29 9:34:53] left: | 0 | ight: | 0
[2019/7/29 9:34:53] left: | 0 | ight: | 0
[2019/7/29 9:34:53] left: | 0 | ight: | 0
[2019/7/29 9:34:53] left: | 0 | ight: | 0
[2019/7/29 9:34:54] left: | 0 | ight: | 0
[2019/7/29 9:34:54] left: | 0 | ight: | 0
[2019/7/29 9:34:54] left: | 0 | ight: | 0
[2019/7/29 9:34:54] left: | 0 | ight: | 0
[2019/7/29 9:34:54] left: | 0 | ight: | 0
[2019/7/29 9:34:54] left: | 0 | ight: | 0
[2019/7/29 9:34:54] left: | 0 | ight: | 0
[2019/7/29 9:34:54] left: | 0 | ight: | 0
[2019/7/29 9:34:54] left: | 0 | ight: | 0
[2019/7/29 9:34:54] left: | 0 | ight: | 0
[2019/7/29 9:34:54] left: | 0 | ight: | 0
[2019/7/29 9:34:54] left: | 0 | ight: | 0
[2019/7/29 9:34:54] left: | 0 | ight: | 0
[2019/7/29 9:34:54] left: | 0 | ight: | 0
[2019/7/29 9:34:54] left: | 0 | ight: | 0
[2019/7/29 9:34:54] left: | 0 | ight: | 0
[2019/7/29 9:34:54] left: | 0 | ight: | 0
[2019/7/29 9:34:54] left: | 0 | ight: | 0
[2019/7/29 9:34:54] left: | 0 | ight: | 0
[2019/7/29 9:34:54] left: | 0 | ight: | 0
[2019/7/29 9:34:54] left: | 0 | ight: | 0
[2019/7/29 9:34:54] left: | 0 | ight: | 0
[2019/7/29 9:34:54] left: | 0 | ight: | 0
[2019/7/29 9:34:54] left: | 0 | ight: | 0
[2019/7/29 9:34:54] left: | 0 | ight: | 0
[2019/7/29 9:34:54] left: | 0 | ight: | 0
[2019/7/29 9:34:54] left: | 0 | ight: | 0
[2019/7/29 9:34:54] left: | 0 | ight: | 0
[2019/7/29 9:34:54] left: | 0 | ight: | 0
[2019/7/29 9:34:54] left: | 0 | ight: | 0
[2019/7/29 9:34:54] left: | 0 | ight: | 0
[2019/7/29 9:34:54] left: | 0 | ight: | 0
[2019/7/29 9:34:54] left: | 0 | ight: | 0
[2019/7/29 9:34:54] left: | 0 | ight: | 0
[2019/7/29 9:34:54] left: | 0 | ight: | 0
[2019/7/29 9:34:54] left: | 0 | ight: | 0
[2019/7/29 9:34:54] left: | 0 | ight: | 0
[2019/7/29 9:34:54] left: | 0 | ight: | 0
[2019/7/29 9:34:54] left: | 0 | ight: | 0
[2019/7/29 9:34:54] left: | 0 | ight: | 0
[2019/7/29 9:34:54] left: | 0 | ight: | 0
[2019/7/29 9:34:54] left: | 0 | ight: | 0
[2019/7/29 9:34:54] left: | 0 | ight: | 0
[2019/7/29 9:34:54] left: | 0 | ight: | 0
[2019/7/29 9:34:54] left: | 0 | ight: | 0
[2019/7/29 9:34:54] left: | 0 | ight: | 0
[2019/7/29 9:34:54] left: | 0 | ight: | 0
[2019/7/29 9:34:54] left: | 0 | ight: | 0
[2019/7/29 9:34:54] left: | 0 | ight: | 0
[2019/7/29 9:34:54] left: | 0 | ight: | 0
[2019/7/29 9:34:54] left: | 0 | ight: | 0
[2019/7/29 9:34:54] left: | 0 | ight: | 0
[2019/7/29 9:34:54] left: | 0 | ight: | 0
[2019/7/29 9:34:54] left: | 0 | ight: | 0
[2019/7/29 9:34:54] left: | 0 | ight: | 0
[2019/7/29 9:34:54] left: | 0 | ight: | 0
[2019/7/29 9:34:54] left: | 0 | ight: | 0
[2019/7/29 9:34:54] left: | 0 | ight: | 0
[2019/7/29 9:34:54] left: | 0 | ight: | 0
[2019/7/29 9:34:54] left: | 0 | ight: | 0
[2019/7/29 9:34:54] left: | 0 | ight: | 0
[2019/7/29 9:34:54] left: | 0 | ight: | 0
[2019/7/29 9:34:54] left: | 0 | ight: | 0
[2019/7/29 9:34:54] left: | 0 | ight: | 0
[2019/7/29 9:34:54] left: | 0 | ight: | 0
[2019/7/29 9:34:54] left: | 0 | ight: | 0
[2019/7/29 9:34:54] left: | 0 | ight: | 0
[2019/7/29 9:34:54] left: | 0 | ight: | 0
[2019/7/29 9:34:54] left: | 0 | ight: | 0
[2019/7/29 9:34:54] left: | 0 | ight: | 0
[2019/7/29 9:34:54] left: | 0 | ight: | 0
[2019/7/29 9:34:54] left: | 0 | ight: | 0
[2019/7/29 9:34:54] left: | 0 | ight: | 0
[2019/7/29 9:34:54] left: | 0 | ight: | 0
[2019/7/29 9:34:54] left: | 0 | ight: | 0
[2019/7/29 9:34:54] left: | 0 | ight: | 0
[2019/7/29 9:34:54] left: | 0 | ight: | 0
[2019/7/29 9:34:54] left: | 0 | ight: | 0
[2019/7/29 9:34:54] left: | 0 | ight: | 0
[2019/7/29 9:34:54] left: | 0 | ight: | 0
[2019/7/29 9:34:54] left: | 0 | ight: | 0
[2019/7/29 9:34:54] left: | 0 | ight: | 0
[2019/7/29 9:34:54] left: | 0 | ight: | 0
[2019/7/29 9:34:54] left: | 0 | ight: | 0
[2019/7/29 9:34:54] left: | 0 | ight: | 0
[2019/7/29 9:34:54] left: | 0 | ight: | 0
[2019/7/29 9:34:54] left: | 0 | ight: | 0
[2019/7/29 9:34:54] left: | 0 | ight: | 0
[2019/7/29 9:34:54] left: | 0 | ight: | 0
[2019/7/29 9:34:54] left: | 0 | ight: | 0
[2019/7/29 9:34:54] left: | 0 | ight: | 0
[2019/7/29 9:34:54] left: | 0 | ight: | 0
[2019/7/29 9:34:54] left: | 0 | ight: | 0
[2019/7/29 9:34:54] left: | 0 | ight: | 0
[2019/7/29 9:34:54] left: | 0 | ight: | 0
[2019/7/29 9:34:54] left: | 0 | ight: | 0
[2019/7/29 9:34:54] left: | 0 | ight: | 0
[2019/7/29 9:34:54] left: | 0 | ight: | 0
[2019/7/29 9:34:54] left: | 0 | ight: | 0
[2019/7/29 9:34:54] left: | 0 | ight: | 0
[2019/7/29 9:34:54] left: | 0 | ight: | 0
[2019/7/29 9:34:54] left: | 0 | ight: | 0
[2019/7/29 9:34:55] left: | 0 | ight: | 0
[2019/7/29 9:34:55] left: | 0 | ight: | 0
[2019/7/29 9:34:55] left: | 0 | ight: | 0
[2019/7/29 9:34:55] left: | 0 | ight: | 0
[2019/7/29 9:34:55] left: | 0 | ight: | 0
[2019/7/29 9:34:55] left: | 0 | ight: | 0
[2019/7/29 9:34:55] left: | 0 | ight: | 0
[2019/7/29 9:34:55] left: | 0 | ight: | 0
[2019/7/29 9:34:55] left: | 0 | ight: | 0
[2019/7/29 9:34:55] left: | 0 | ight: | 0
[2019/7/29 9:34:55] left: | 0 | ight: | 0
[2019/7/29 9:34:55] left: | 0 | ight: | 0
[2019/7/29 9:34:55] left: | 0 | ight: | 0
[2019/7/29 9:34:55] left: | 0 | ight: | 0
[2019/7/29 9:34:55] left: | 0 | ight: | 0
[2019/7/29 9:34:55] left: | 0 | ight: | 0
[2019/7/29 9:34:55] left: | 0 | ight: | 0
[2019/7/29 9:34:55] left: | 0 | ight: | 0
[2019/7/29 9:34:55] left: | 0 | ight: | 0
[2019/7/29 9:34:55] left: | 0 | ight: | 0
[2019/7/29 9:34:55] left: | 0 | ight: | 0
[2019/7/29 9:34:55] left: | 0 | ight: | 0
[2019/7/29 9:34:55] left: | 0 | ight: | 0
[2019/7/29 9:34:55] left: | 0 | ight: | 0
[2019/7/29 9:34:55] left: | 0 | ight: | 0
[2019/7/29 9:34:55] left: | 0 | ight: | 0
[2019/7/29 9:34:55] left: | 0 | ight: | 0
[2019/7/29 9:34:55] left: | 0 | ight: | 0
[2019/7/29 9:34:55] left: | 0 | ight: | 0
[2019/7/29 9:34:55] left: | 0 | ight: | 0
[2019/7/29 9:34:55] left: | 0 | ight: | 0
[2019/7/29 9:34:55] left: | 0 | ight: | 0
[2019/7/29 9:34:55] left: | 0 | ight: | 0
[2019/7/29 9:34:55] left: | 0 | ight: | 0
[2019/7/29 9:34:55] left: | 0 | ight: | 0
[2019/7/29 9:34:55] left: | 0 | ight: | 0
[2019/7/29 9:34:55] left: | 0 | ight: | 0
[2019/7/29 9:34:55] left: | 0 | ight: | 0
[2019/7/29 9:34:55] left: | 0 | ight: | 0
[2019/7/29 9:34:55] left: | 0 | ight: | 0
[2019/7/29 9:34:55] left: | 0 | ight: | 0
[2019/7/29 9:34:55] left: | 0 | ight: | 0
[2019/7/29 9:34:55] left: | 0 | ight: | 0
[2019/7/29 9:34:55] left: | 0 | ight: | 0
[2019/7/29 9:34:55] left: | 0 | ight: | 0
[2019/7/29 9:34:55] left: | 0 | ight: | 0
[2019/7/29 9:34:55] left: | 0 | ight: | 0
[2019/7/29 9:34:55] left: | 0 | ight: | 0
[2019/7/29 9:34:55] left: | 0 | ight: | 0
[2019/7/29 9:34:55] left: | 0 | ight: | 0
[2019/7/29 9:34:55] left: | 0 | ight: | 0
[2019/7/29 9:34:55] left: | 0 | ight: | 0
[2019/7/29 9:34:55] left: | 0 | ight: | 0
[2019/7/29 9:34:55] left: | 0 | ight: | 0
[2019/7/29 9:34:55] left: | 0 | ight: | 0
[2019/7/29 9:34:55] left: | 0 | ight: | 0
[2019/7/29 9:34:55] left: | 0 | ight: | 0
[2019/7/29 9:34:55] left: | 0 | ight: | 0
[2019/7/29 9:34:55] left: | 0 | ight: | 0
[2019/7/29 9:34:55] left: | 0 | ight: | 0
[2019/7/29 9:34:55] left: | 0 | ight: | 0
[2019/7/29 9:34:55] left: | 0 | ight: | 0
[2019/7/29 9:34:55] left: | 0 | ight: | 0
[2019/7/29 9:34:55] left: | 0 | ight: | 0
[2019/7/29 9:34:55] left: | 0 | ight: | 0
[2019/7/29 9:34:55] left: | 0 | ight: | 0
[2019/7/29 9:34:55] left: | 0 | ight: | 0
[2019/7/29 9:34:55] left: | 0 | ight: | 0
[2019/7/29 9:34:55] left: | 0 | ight: | 0
[2019/7/29 9:34:55] left: | 0 | ight: | 0
[2019/7/29 9:34:55] left: | 0 | ight: | 0
[2019/7/29 9:34:55] left: | 0 | ight: | 0
[2019/7/29 9:34:55] left: | 0 | ight: | 0
[2019/7/29 9:34:55] left: | 0 | ight: | 0
[2019/7/29 9:34:55] left: | 0 | ight: | 0
[2019/7/29 9:34:55] left: | 0 | ight: | 0
[2019/7/29 9:34:55] left: | 0 | ight: | 0
[2019/7/29 9:34:55] left: | 0 | ight: | 0
[2019/7/29 9:34:55] left: | 0 | ight: | 0
[2019/7/29 9:34:55] left: | 0 | ight: | 0
[2019/7/29 9:34:55] left: | 0 | ight: | 0
[2019/7/29 9:34:55] left: | 0 | ight: | 0
[2019/7/29 9:34:55] left: | 0 | ight: | 0
[2019/7/29 9:34:55] left: | 0 | ight: | 0
[2019/7/29 9:34:55] left: | 0 | ight: | 0
[2019/7/29 9:34:55] left: | 0 | ight: | 0
[2019/7/29 9:34:55] left: | 0 | ight: | 0
[2019/7/29 9:34:55] left: | 0 | ight: | 0
[2019/7/29 9:34:55] left: | 0 | ight: | 0
[2019/7/29 9:34:55] left: | 0 | ight: | 0
[2019/7/29 9:34:55] left: | 0 | ight: | 0
[2019/7/29 9:34:55] left: | 0 | ight: | 0
[2019/7/29 9:34:55] left: | 0 | ight: | 0
[2019/7/29 9:34:55] left: | 0 | ight: | 0
[2019/7/29 9:34:55] left: | 0 | ight: | 0
[2019/7/29 9:34:55] left: | 0 | ight: | 0
[2019/7/29 9:34:55] left: | 0 | ight: | 0
[2019/7/29 9:34:55] left: | 0 | ight: | 0
[2019/7/29 9:34:55] left: | 0 | ight: | 0
[2019/7/29 9:34:55] left: | 0 | ight: | 0
[2019/7/29 9:34:55] left: | 0 | ight: | 0
[2019/7/29 9:34:56] left: | 0 | ight: | 0
[2019/7/29 9:34:56] left: | 0 | ight: | 0
[2019/7/29 9:34:56] left: | 0 | ight: | 0
[2019/7/29 9:34:56] left: | 0 | ight: | 0
[2019/7/29 9:34:56] left: | 0 | ight: | 0
[2019/7/29 9:34:56] left: | 0 | ight: | 0
[2019/7/29 9:34:56] left: | 0 | ight: | 0
[2019/7/29 9:34:56] left: | 1 | ight: | 1
[2019/7/29 9:34:56] left: | 3 | ight: | 3
[2019/7/29 9:34:56] left: | 5 | ight: | 5
[2019/7/29 9:34:56] left: | 7 | ight: | 7
[2019/7/29 9:34:56] left: | 9 | ight: | 9
[2019/7/29 9:34:56] left: | 11 | ight: | 11
[2019/7/29 9:34:56] left: | 11 | ight: | 11
[2019/7/29 9:34:56] left: | 11 | ight: | 11
[2019/7/29 9:34:56] left: | 11 | ight: | 11
[2019/7/29 9:34:56] left: | 11 | ight: | 11
[2019/7/29 9:34:56] left: | 11 | ight: | 11
[2019/7/29 9:34:56] left: | 11 | ight: | 11
[2019/7/29 9:34:56] left: | 14 | ight: | 14
[2019/7/29 9:34:56] left: | 14 | ight: | 14
[2019/7/29 9:34:56] left: | 14 | ight: | 14
[2019/7/29 9:34:56] left: | 14 | ight: | 14
[2019/7/29 9:34:56] left: | 14 | ight: | 14
[2019/7/29 9:34:56] left: | 14 | ight: | 14
[2019/7/29 9:34:56] left: | 14 | ight: | 14
[2019/7/29 9:34:56] left: | 14 | ight: | 14
[2019/7/29 9:34:56] left: | 14 | ight: | 14
[2019/7/29 9:34:56] left: | 13 | ight: | 13
[2019/7/29 9:34:56] left: | 15 | ight: | 15
[2019/7/29 9:34:56] left: | 17 | ight: | 17
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

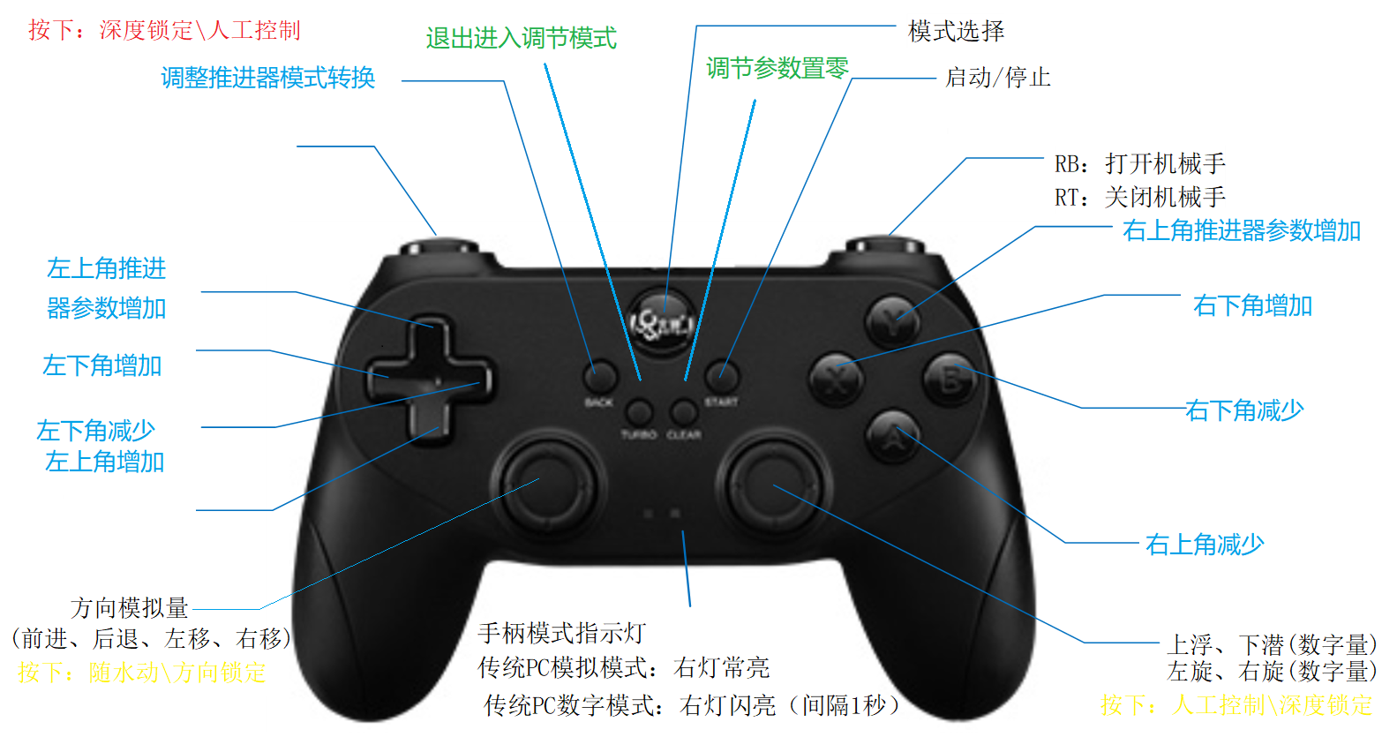
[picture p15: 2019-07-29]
docs/协定/手柄按键调试定义.png

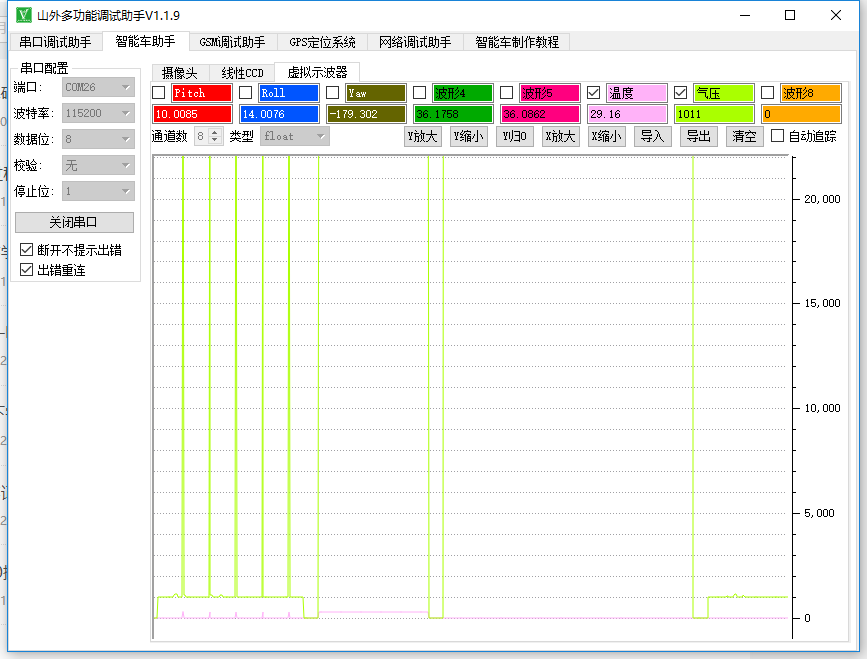
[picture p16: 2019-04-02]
docs/调试记录/MS5837记录.png

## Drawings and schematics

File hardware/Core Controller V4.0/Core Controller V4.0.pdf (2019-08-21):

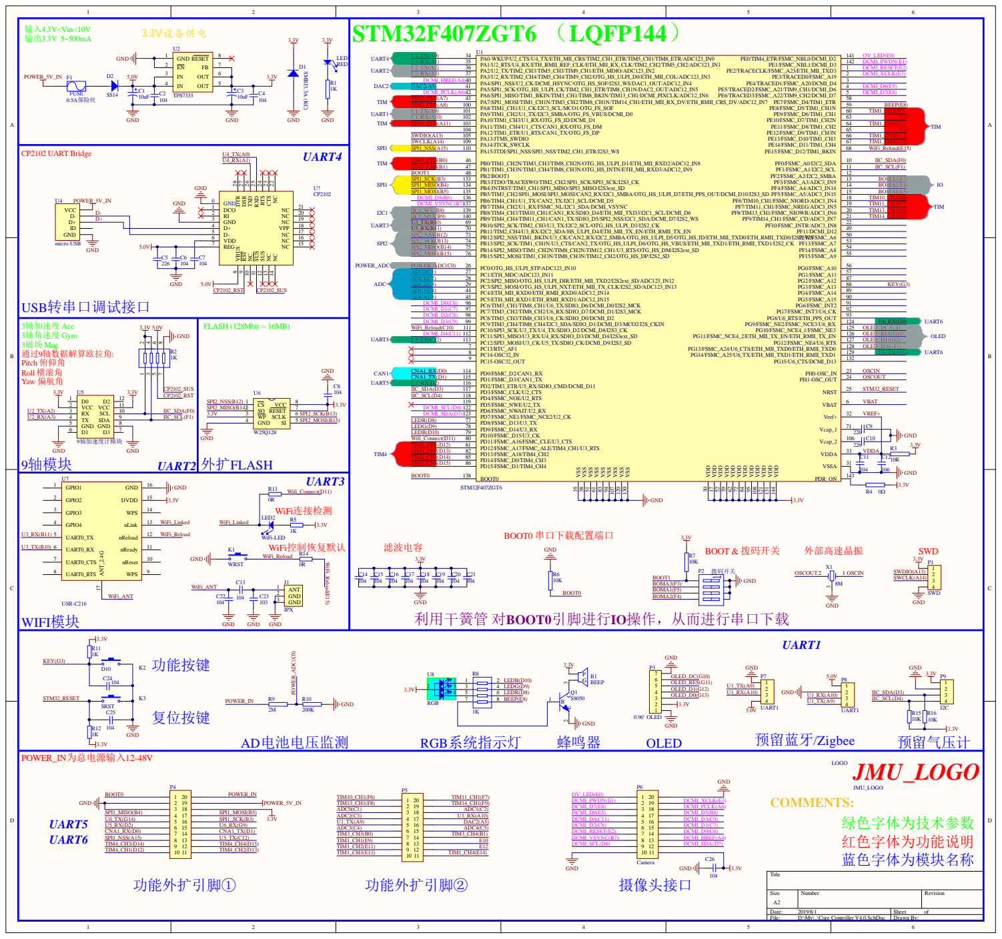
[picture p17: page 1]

输入4.3V<Vin<10V 3.3V设备供电 输出3.3V 5~500mA 3.3V 3.3V U2 | STM32F407ZGT6 （LQFP144） U1

Size A2 | Number | Revision

Date: 2019/8/1 | Sheet of
File: D:\My\..\Core Controller V4.0.SchDoc | Drawn By:

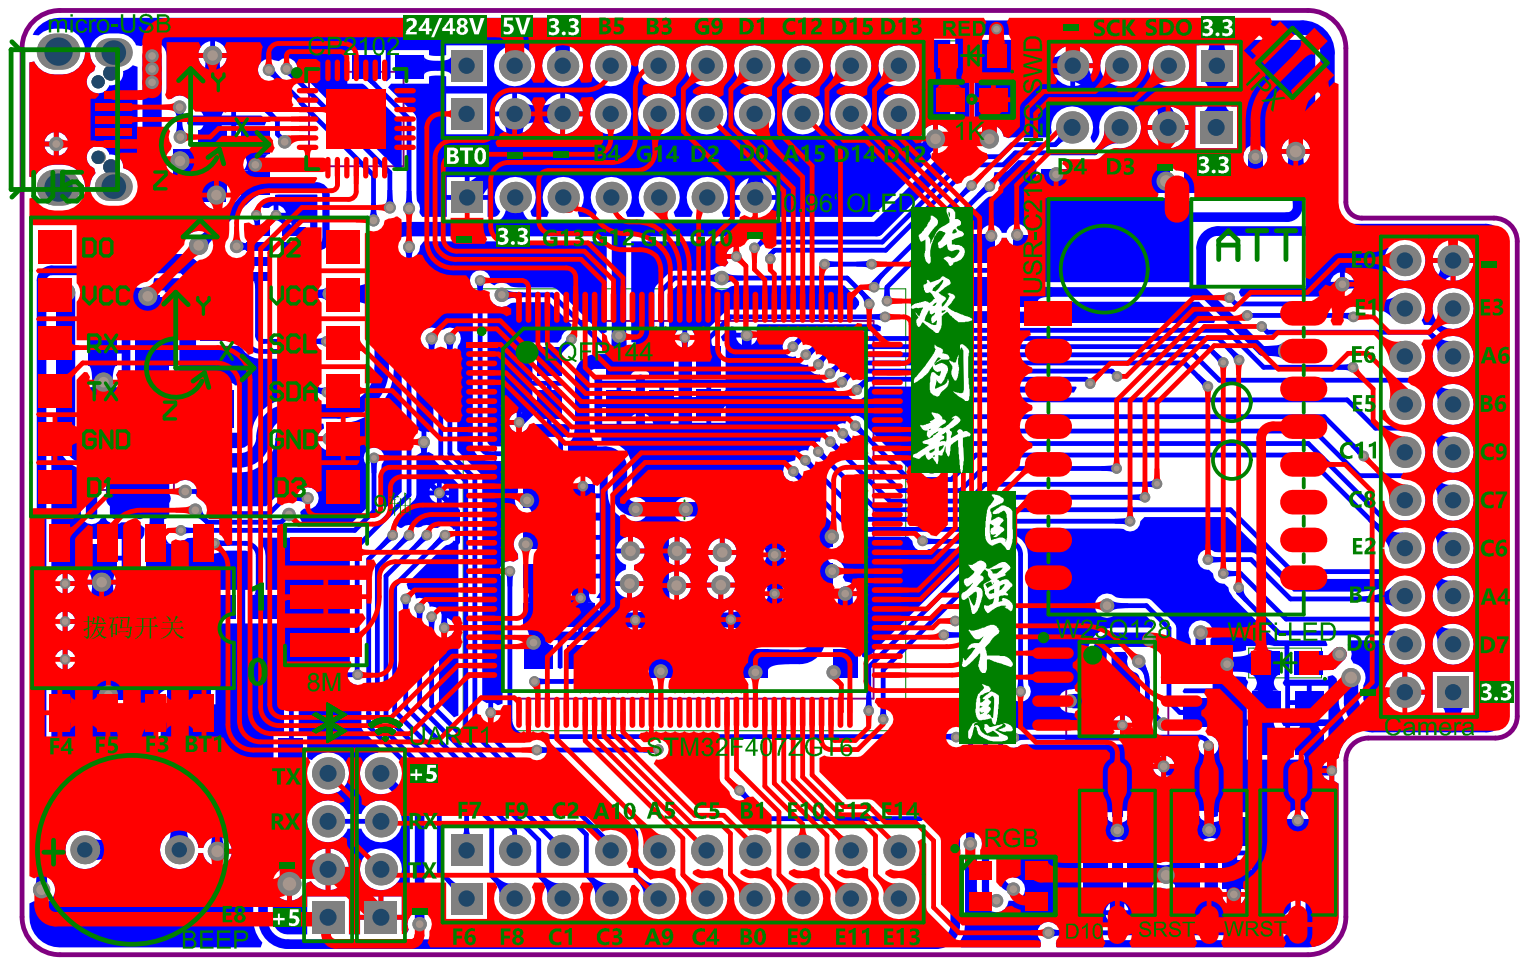
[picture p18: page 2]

Comment | Description | Designator | Footprint | LibRef | Quantity
BEEP | | B1 | BUZZER | BEEP | 1
10uF | 极性贴片电容 | C1, C3 | TAJ-A | Pol Cap | 2
104 | 无极贴片电容, 无极贴片 电容, 无极贴片电容, 无 极贴片电容, 无极贴片电 容, [NoValue], 无极贴片 电容, [NoValue], [NoValue], [NoValue], [NoValue], [NoValue], [NoValue], [NoValue], [NoValue], 无极贴片电 容, [NoValue], [NoValue], 无极贴片电 容 | C2, C4, C6, C7, C8, C11, C13, C14, C15, C16, C17, C18, C19, C20, C21, C22, C24, C25, C26 | 0805C | Cap1, Cap1, Cap1, Cap1, Cap1, C1, Cap1, C1, C1, C1, C1, C1, C1, C1, C1, Cap1, C1, C1, Cap1 | 19
226 | 无极贴片电容, [NoValue], [NoValue] | C5, C9, C10 | 0805C | Cap1, C1, C1 | 3
106 | | C12 | 0805C | C1 | 1
103 | 无极贴片电容 | C23 | 0805C | Cap1 | 1
SMBJ3.3A (KC) | 二极管 | D1 | SMBJ | Diode | 1
SS14 | 二极管 | D2 | SMA/DO-214AC | Diode | 1
0.5A保险丝 | 保险丝 | F1 | 1206R | Fuse | 1
IPX | | J1 | IPX天线底座 | IPX天线座 | 1
WRST | 轻触开关 | K1 | 贴片按键 | 轻触按键 | 1
D10 | | K2 | 贴片按键 | Key(两脚贴片) | 1
SRST | | K3 | 贴片按键 | Key(两脚贴片) | 1
RED | 发光二极管 | LED1 | 0805LED(RED) | LED | 1
WiFi-LED | 发光二极管 | LED2 | 0805LED(GREEN) | LED | 1
JMU_LOGO | LOGO | LOGO | JMU_LOGO(1.35cm) | JMU_LOGO | 1
SWD | 排针 | P1 | Header 4 | Header 4 | 1
拨码开关 | 4位拨码开关 | P2 | 拨码开关(4位贴片) | 拨码开关4 | 1
0.96‘ OLED | 排针 | P3 | Header 7 | Header 7 | 1
| | P4, P5 | Header 10X2 | Header 10X2 | 2
Camera | | P6 | Header 10X2 | Header 10X2 | 1
UART1 | 排针 | P7, P8 | Header 4(排母) | Header 4 | 2
I2C | 排针 | P9 | Header 4(排母) | Header 4 | 1
S8050 | NPN三极管 | Q1 | SOT-23 | NPN | 1
1K | [NoValue], 电阻, 电阻, 电阻 | R1, R5, R11, R12 | 0805R | R1, Res, Res, Res | 4
1K | 排阻 | R2, R8 | 排阻(4位贴片) | Res-4 | 2
10R | | R3 | 0805R | R1 | 1
0Ω | | R4 | 0805R | R1 | 1
10K | [NoValue], [NoValue], 电阻, 电阻 | R6, R7, R15, R16 | 0805R | R1, R1, Res, Res | 4
2M | | R9 | 0805R | R1 | 1
200K | | R10 | 0805R | R1 | 1
0R | 电阻 | R13, R14 | 0805R | Res | 2
STM32F407ZGT6 | | U1 | LQFP-144 | STM32F407ZET6 | 1
TPS7333 | 3.3V电源芯片 | U2 | SOP-8 | TPS7333 | 1
micro-USB | USB接口 | U4 | Micro-USB (兼容牛角) | micro-USB | 1
9轴加速度计模块 | | U5 | 9轴加速度计 | 9轴加速度计 | 1
W25Q128 | FLASH芯片 | U6 | SOW-8 | W25Q128 | 1
USR-C216 | | U7 | USR-C216 | USR-C216 | 1
RGB | | U8 | RGB-3528 | RGB | 1
CP2102 | USB转串口芯片 | U? | QFN-28 | CP2102 | 1
8M | | X1 | 三脚贴片8M晶振 | XTAL三脚贴片晶振 | 1

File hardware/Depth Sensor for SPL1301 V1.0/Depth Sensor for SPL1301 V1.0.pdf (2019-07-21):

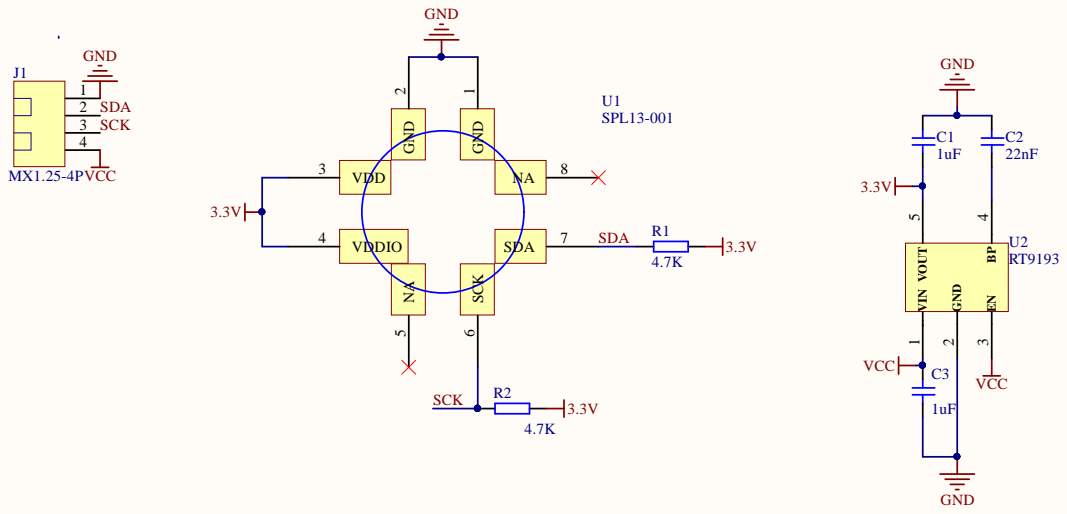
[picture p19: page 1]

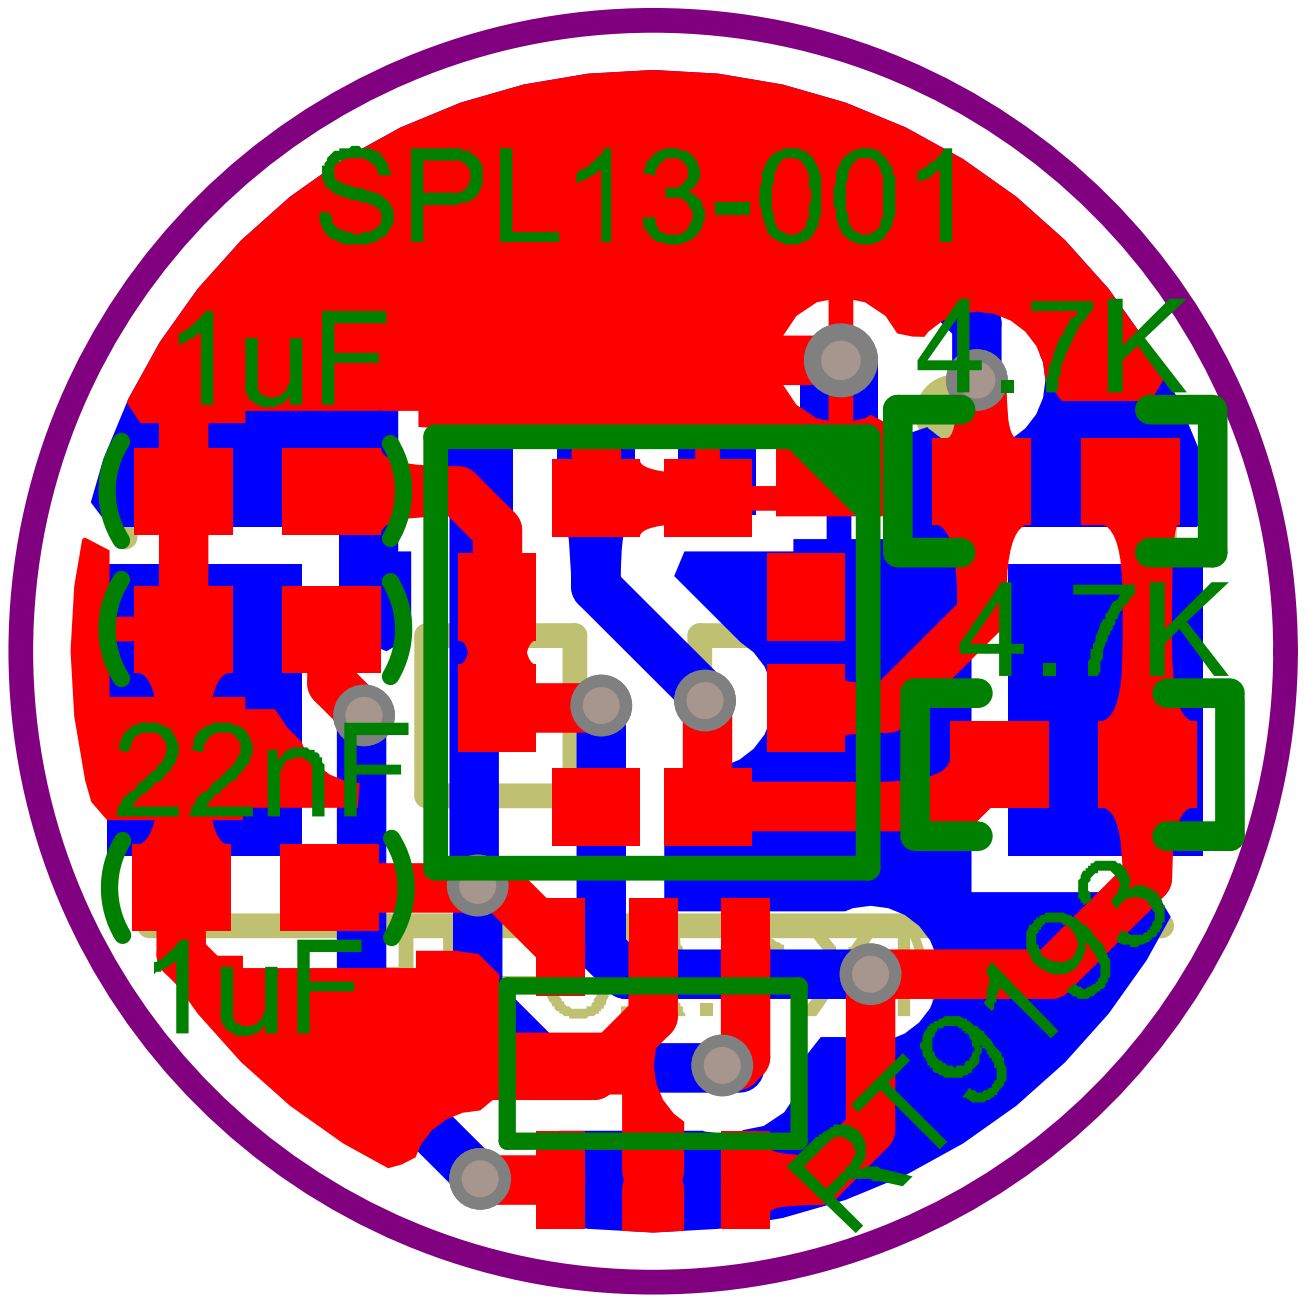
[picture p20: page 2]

Comment | Description | Designator | Footprint | LibRef | Quantity
1uF | 无极贴片电容 | C1, C3 | 0603C | Cap1 | 2
22nF | 无极贴片电容 | C2 | 0603C | Cap1 | 1
MX1.25-4P | | J1 | MX1.25-4P | MX1.25-4P_1 | 1
4.7K | 电阻 | R1, R2 | 0603R | Res | 2
SPL13-001 | | U1 | SPL13-001 | SPL13-001_1 | 1
RT9193 | | U2 | RT9193 | RT9193 | 1

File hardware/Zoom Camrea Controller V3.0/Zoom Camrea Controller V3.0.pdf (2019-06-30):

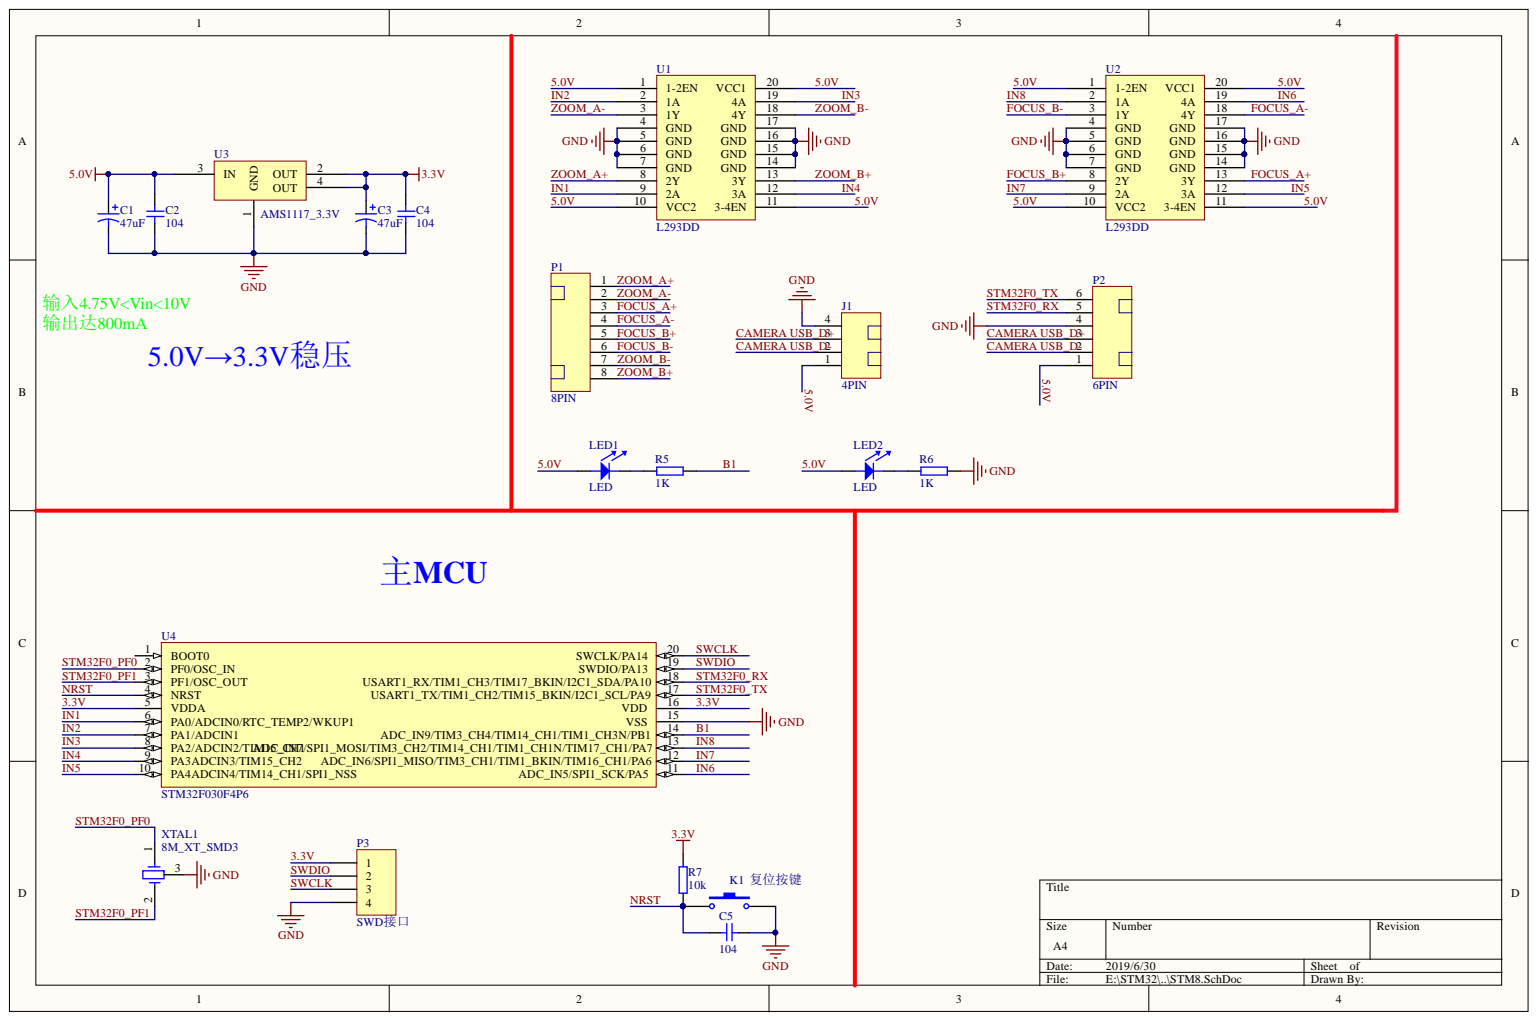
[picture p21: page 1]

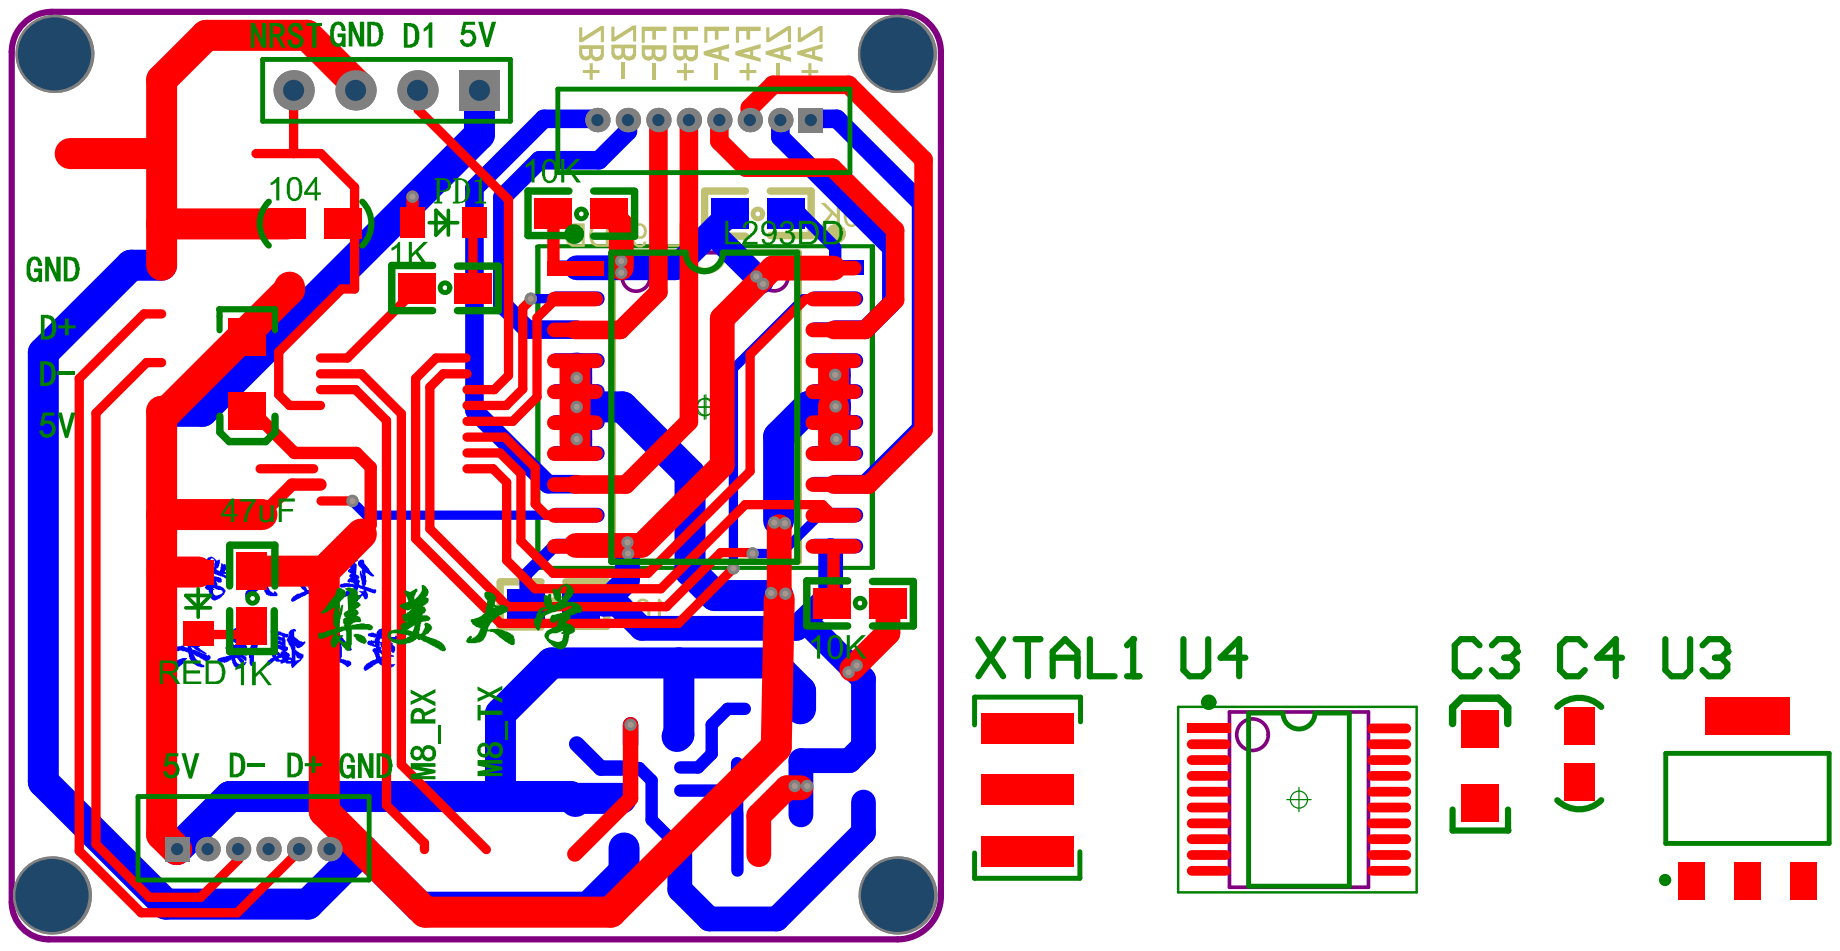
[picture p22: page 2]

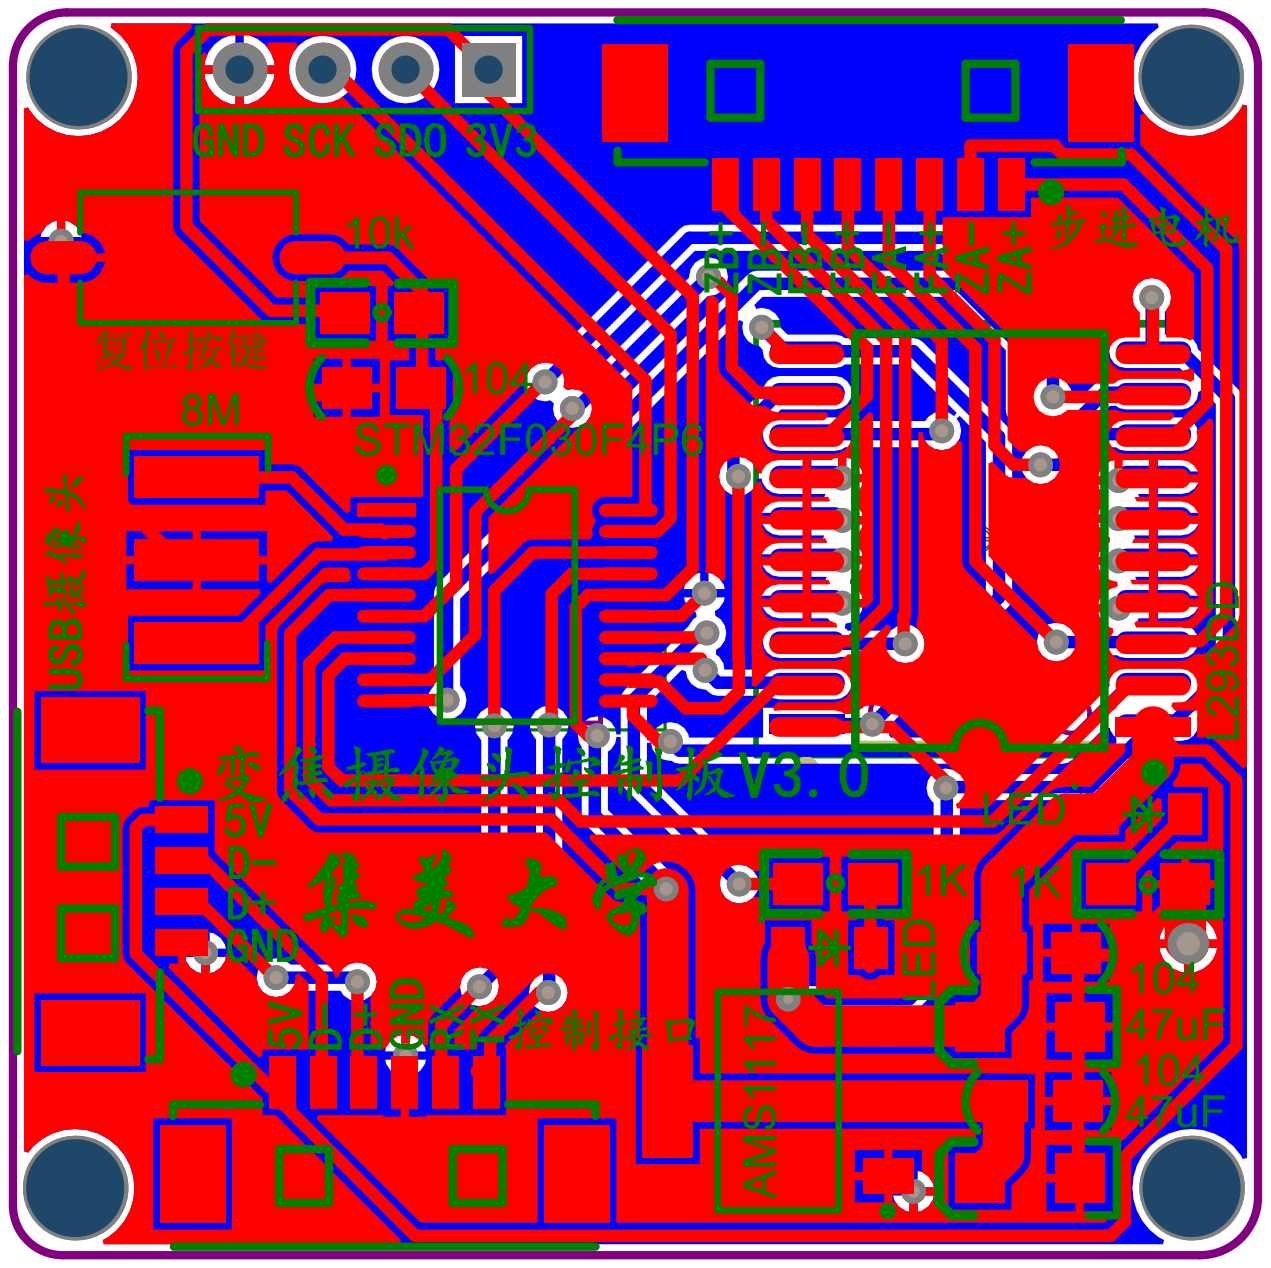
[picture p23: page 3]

Comment | Description | Designator | Footprint | LibRef | Quantity
47uF | 极性贴片电容 | C1, C3 | TAJ-A | Pol Cap | 2
104 | 无极贴片电容 | C2, C4, C5 | 0805C | Cap1 | 3
4PIN | | J1 | MX1.25WS-4P | MX1.25-4P | 1
复位按键 | 轻触开关 | K1 | 贴片按键 | 贴片按键 | 1
LED | 发光二极管 | LED1, LED2 | 0805LED(RED) | LED | 2
8PIN | | P1 | MX1.25WS-8P | MX1.25-8P | 1
6PIN | | P2 | MX1.25WS-6P | MX1.25-6P | 1
SWD接口 | Header, 4-Pin | P3 | Header 4 | Header 4 | 1
1K | 电阻 | R5, R6 | 0805R | Res | 2
10k | 电阻 | R7 | 0805R | Res | 1
L293DD | | U1, U2 | SOP-20 | L293D | 2
AMS1117_3.3V | 电源芯片 | U3 | SOT-223 | AMS1117-3.3V/5.0V | 1
STM32F030F4P6 | ARM Cortex-M0 32-bit MCU, 16 KB Flash, 4 KB Internal RAM, 15 I/Os, 20-pin TSSOP, -40 to 85 degC, Tube | U4 | STM32F030 | STM32F030F4P6 | 1
8M_XT_SMD3 | | XTAL1 | 三脚贴片8M晶振 | XTAL三脚贴片晶振 | 1

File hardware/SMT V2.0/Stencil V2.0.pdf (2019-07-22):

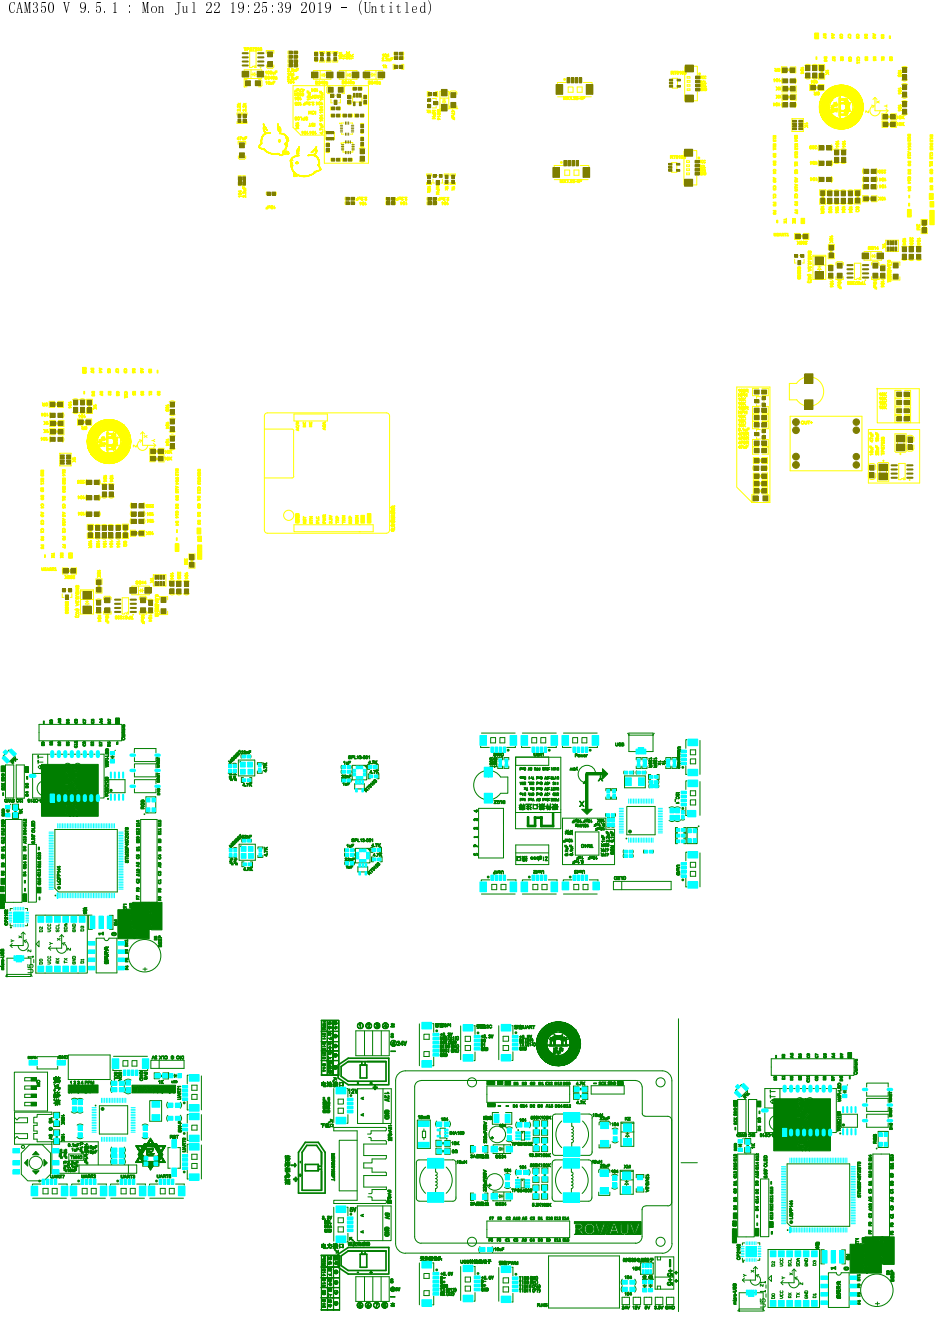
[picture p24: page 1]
CAM350 V 9.5.1 : Mon Jul 22 19:25:39 2019 -; (Untitled)

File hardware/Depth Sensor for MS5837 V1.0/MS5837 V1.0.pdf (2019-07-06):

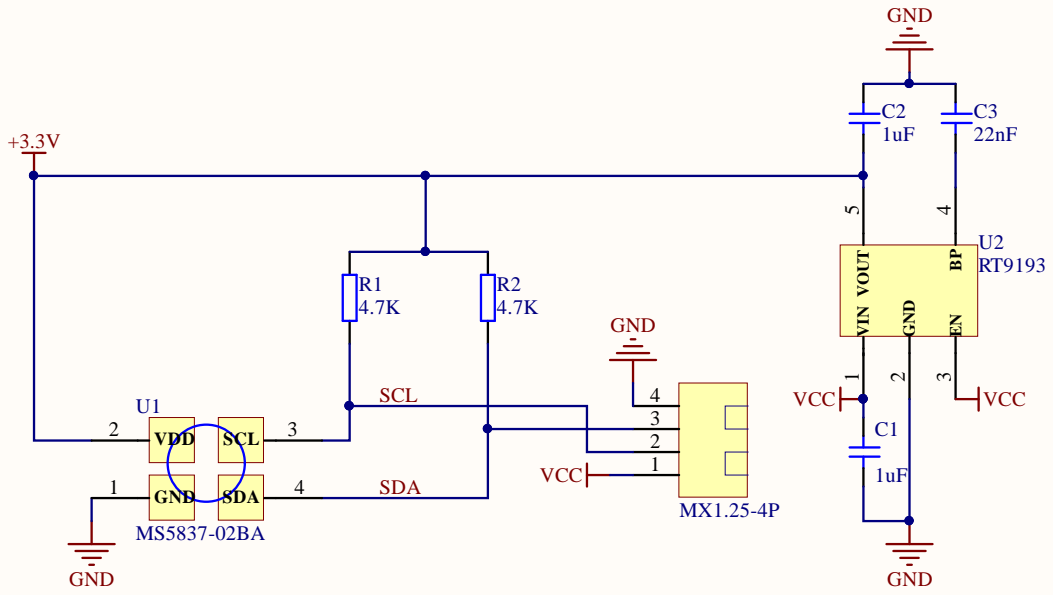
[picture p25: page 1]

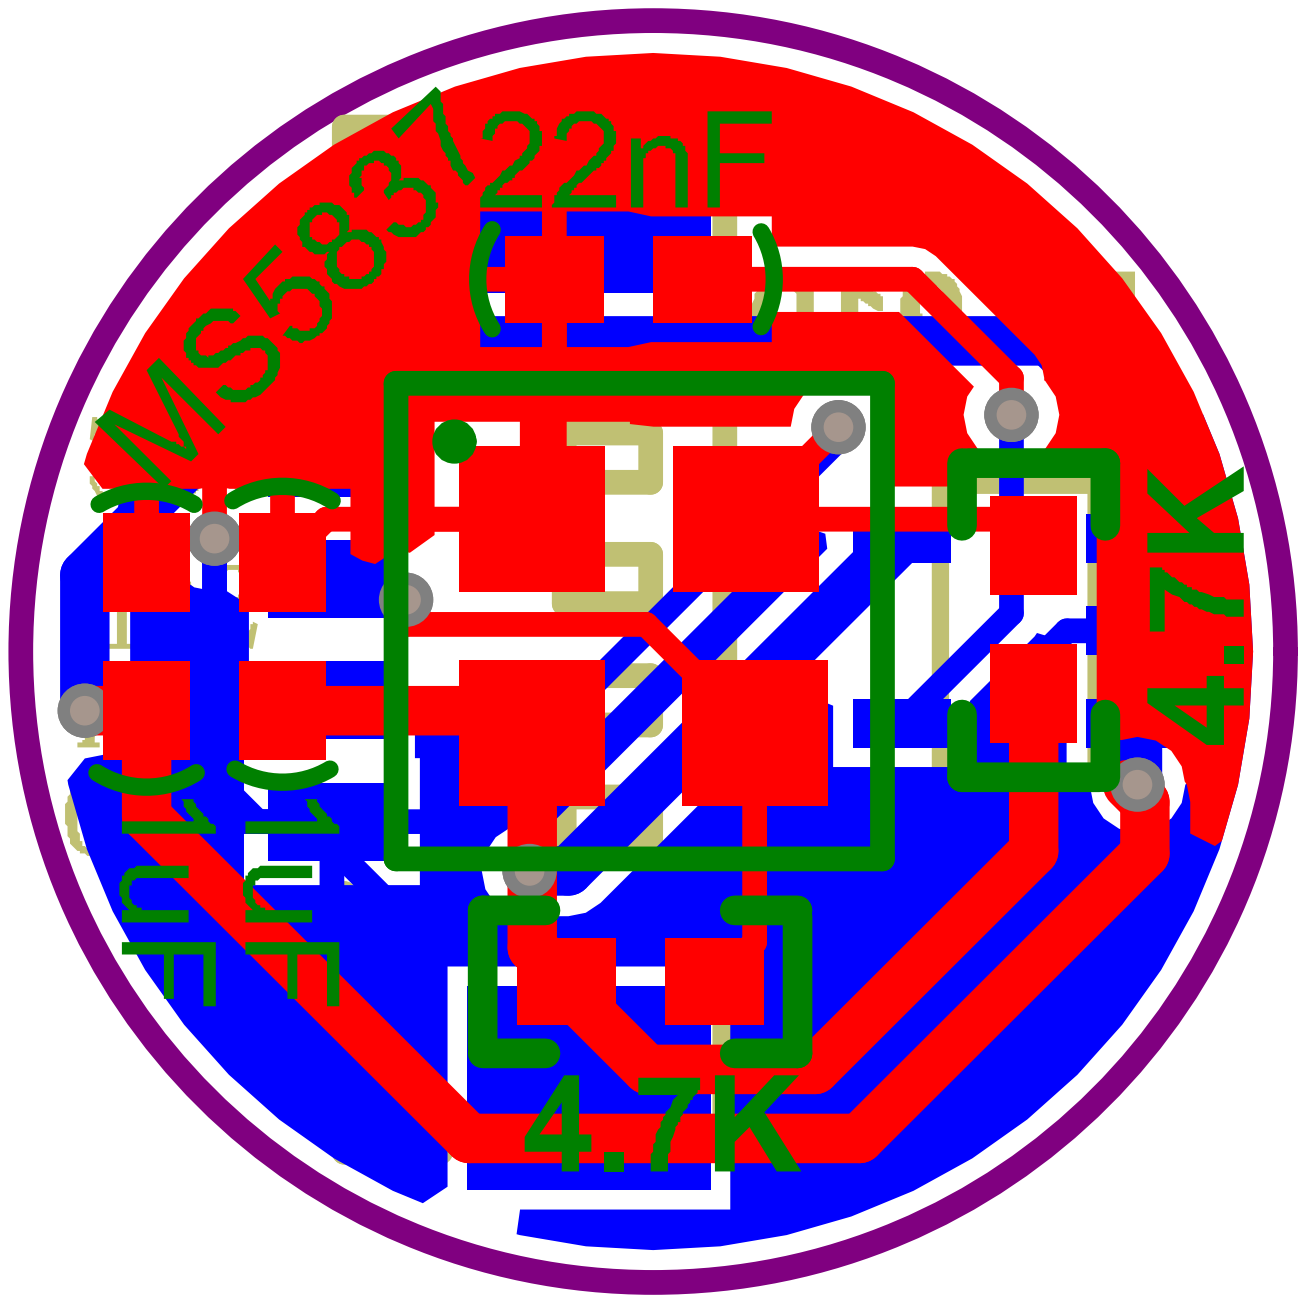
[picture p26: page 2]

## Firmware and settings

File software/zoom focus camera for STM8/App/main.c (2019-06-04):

#include "stm8s_gpio.h"
#include "bsp_timer.h"
#include "motor.h"
#include "key.h"
#include "stm8s_it.h"
#include "bsp_flash.h"
#include "bsp_uart.h"

extern uint8_t motor_data[6];//接收数据包
extern bool recvl_data_ok;//数据接收成功

uint8_t WriteBuf[6]={ 1 , 1 , 1 , 1 , 1 , 1 };
//uint8_t Camera_Limit_Zoom_Data[6]={0xAA,0x55,0x02,0xFF,0x00,0x00};
//uint8_t Camera_Limit_Focus_Data[6]={0xAA,0x55,0x02,0x00,0xFF,0x00};
bool rotate_Zoom=FALSE; 
bool rotate_Focus=FALSE; 
bool scope_ok=FALSE;

void data_handle();

void main(void)
{
  TIMER_Initializes();
  STEP_Init();
  UART_Initializes();
 
  while(1)
  {
   data_handle();  
  }
}

void data_handle(void)
{

 if(recvl_data_ok)
   {

    // UART1_SendNByte(WriteBuf,6);
    if(motor_data[3]==0x01||motor_data[3]==0x02)     //选择不同步进机
    {
      switch(motor_data[3])
      {
         case 0x01:rotate_Zoom=FALSE;WriteBuf[0]-=1;break;  //控制是正转还是反转
         case 0x02:rotate_Zoom=TRUE;WriteBuf[0]+=1;break;
         default: break;
      }
      
      if(WriteBuf[0]== 0 )
      {
        if(WriteBuf[1]== 1 &&WriteBuf[2]== 1 )
        {
          WriteBuf[0]= 1 ;
        }
        else
       {
         WriteBuf[0]= 8 ;
         WriteBuf[1]-=1;
         if(WriteBuf[1]== 0 )
         {
           WriteBuf[1]= 8 ;
           WriteBuf[2]-=1;          
         }
         scope_ok=TRUE;       
       }
      }
      else if(WriteBuf[0]== 9 )
      {

        if(WriteBuf[1]== 8 &&WriteBuf[2]== 8 )
        {
          WriteBuf[0]= 8 ;      
        }
        else
        {
          WriteBuf[0]= 1 ;
          WriteBuf[1]+=1;
          if(WriteBuf[1]== 9 )
         {
           WriteBuf[1]= 1 ;
           WriteBuf[2]+=1;          
         }
         scope_ok=TRUE;          
        }
      }
      else scope_ok=TRUE;
      
      if(scope_ok) 
      {
        MotorNAngle(ZOOM_MOTOR,1,rotate_Zoom);
        UART1_SendNByte(WriteBuf,6);
        motor_data[3]=0x00;
      }
    }
    else if(motor_data[3]==0x88)
    {
     MotorNCircle(ZOOM_MOTOR,1,TRUE);
     WriteBuf[0]= 8 ;
     WriteBuf[1]= 8 ;
     WriteBuf[2]= 8 ;
     UART1_SendNByte(WriteBuf,6);
     motor_data[3]=0x00;
    }

    
    if(motor_data[4]==0x01||motor_data[4]==0x02)
    {
      switch(motor_data[4])
      {
         case 0x01:rotate_Focus=FALSE;WriteBuf[3]-=1;break;  //控制是正转还是反转
         case 0x02:rotate_Focus=TRUE;WriteBuf[3]+=1;break;
         default: break;
      }
      
      if(WriteBuf[3]== 0 )
      {
        if(WriteBuf[4]== 1 &&WriteBuf[5]== 1 )
        {
          WriteBuf[3]= 1 ;
        }
        else
       {
         WriteBuf[3]= 8 ;
         WriteBuf[4]-=1;
         if(WriteBuf[4]== 0 )
         {
           WriteBuf[4]= 8 ;
           WriteBuf[5]-=1;          
         }
         scope_ok=TRUE;       
       }
      }
      else if(WriteBuf[3]== 9 )
      {
        if(WriteBuf[4]== 8 &&WriteBuf[5]== 8 )
        {
          WriteBuf[3]= 8 ;    
        }
        else
        {
          WriteBuf[3]= 1 ;
          WriteBuf[4]+=1;
          if(WriteBuf[4]== 9 )
         {
           WriteBuf[4]= 1 ;
           WriteBuf[5]+=1;          
         }
         scope_ok=TRUE;          
        }
      }
      else scope_ok=TRUE;
      
      if(scope_ok) 
       {
          MotorNAngle(FOCUS_MOTOR,1,rotate_Focus);
          UART1_SendNByte(WriteBuf,6);
          motor_data[4]=0x00;
       }
    }
    else if(motor_data[4]==0x88)
    {
     MotorNCircle(FOCUS_MOTOR,1,TRUE);
     WriteBuf[3]= 8 ;
     WriteBuf[4]= 8 ;
     WriteBuf[5]= 8 ;
     UART1_SendNByte(WriteBuf,6);
     motor_data[4]=0x00;
    }
   }
 else {
 
    STEP_Stop();
 }
}


#ifdef USE_FULL_ASSERT                           //断言(参考官方)

void assert_failed(u8* file, u32 line)
{
  /* User can add his own implementation to report the file name and line number,
     ex: printf("Wrong parameters value: file %s on line %d\r\n", file, line) */

  /* Infinite loop */
  while (1)
  {}
}
#endif


/**** Copyright (C)2017 strongerHuang. All Rights Reserved **** END OF FILE ****/

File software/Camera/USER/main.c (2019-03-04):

#include "sys.h"
#include "delay.h"
#include "usart.h"
#include "led.h"
#include "key.h"
#include "usmart.h"  
#include "usart2.h"  
#include "timer.h" 
#include "ov2640.h" 
#include "dcmi.h" 
//ALIENTEK 探索者STM32F407开发板 实验35
//摄像头 实验 -库函数版本
//技术支持：www.openedv.com
//淘宝店铺：http://eboard.taobao.com  
//广州市星翼电子科技有限公司  
//作者：正点原子 @ALIENTEK

u8 ov2640_mode=1;						//工作模式:0,RGB565模式;1,JPEG模式

#define jpeg_buf_size 10*1024//31*1024  			//定义JPEG数据缓存jpeg_buf的大小(*4字节)
__align(4) u32 jpeg_buf[jpeg_buf_size];	//JPEG数据缓存buf
volatile u32 jpeg_data_len=0; 			//buf中的JPEG有效数据长度 
volatile u8 jpeg_data_ok=0;				//JPEG数据采集完成标志 
										//0,数据没有采集完;
										//1,数据采集完了,但是还没处理;
										//2,数据已经处理完成了,可以开始下一帧接收
//JPEG尺寸支持列表
const u16 jpeg_img_size_tbl[][2]=
{
	176,144,	//QCIF
	160,120,	//QQVGA
	352,288,	//CIF
	320,240,	//QVGA
	640,480,	//VGA
	800,600,	//SVGA
	1024,768,	//XGA
	1280,1024,	//SXGA
	1600,1200,	//UXGA
}; 
const u8*EFFECTS_TBL[7]={"Normal","Negative","B&W","Redish","Greenish","Bluish","Antique"};	//7种特效 
const u8*JPEG_SIZE_TBL[9]={"QCIF","QQVGA","CIF","QVGA","VGA","SVGA","XGA","SXGA","UXGA"};	//JPEG图片 9种尺寸 


//处理JPEG数据
//当采集完一帧JPEG数据后,调用此函数,切换JPEG BUF.开始下一帧采集.
void jpeg_data_process(void)
{
	if(ov2640_mode)//只有在JPEG格式下,才需要做处理.
	{
		if(jpeg_data_ok==0)	//jpeg数据还未采集完?
		{	
			DMA_Cmd(DMA2_Stream1, DISABLE);//停止当前传输 
			while (DMA_GetCmdStatus(DMA2_Stream1) != DISABLE){}//等待DMA2_Stream1可配置  
			jpeg_data_len=jpeg_buf_size-DMA_GetCurrDataCounter(DMA2_Stream1);//得到此次数据传输的长度
				
			jpeg_data_ok=1; 				//标记JPEG数据采集完按成,等待其他函数处理
		}
		if(jpeg_data_ok==2)	//上一次的jpeg数据已经被处理了
		{
				DMA2_Stream1->NDTR=jpeg_buf_size;	
				DMA_SetCurrDataCounter(DMA2_Stream1,jpeg_buf_size);//传输长度为jpeg_buf_size*4字节
				DMA_Cmd(DMA2_Stream1, ENABLE);			//重新传输
				jpeg_data_ok=0;						//标记数据未采集
		}
	}
} 
//JPEG测试
//JPEG数据,通过串口2发送给电脑.
void jpeg_test(void)
{
	u32 i; 
	u8 *p;
	u8 effect=0,saturation=2,contrast=2;
	u8 size=4;		//默认是QVGA 320*240尺寸
	u8 msgbuf[15];	//消息缓存区 

	sprintf((char*)msgbuf,"JPEG Size:%s",JPEG_SIZE_TBL[size]);
	printf("%s\r\n",msgbuf);
	
 	OV2640_JPEG_Mode();		//JPEG模式
	My_DCMI_Init();			//DCMI配置
	DCMI_DMA_Init((u32)&jpeg_buf,jpeg_buf_size,DMA_MemoryDataSize_Word,DMA_MemoryInc_Enable);//DCMI DMA配置   
	OV2640_OutSize_Set(jpeg_img_size_tbl[size][0],jpeg_img_size_tbl[size][1]);//设置输出尺寸 
	DCMI_Start(); 		//启动传输
	while(1)
	{
		if(jpeg_data_ok==1)	//已经采集完一帧图像了
		{  
			p=(u8*)jpeg_buf;
			//LCD_ShowString(30,210,210,16,16,"Sending JPEG data..."); //提示正在传输数据
			for(i=0;i<jpeg_data_len*4;i++)		//dma传输1次等于4字节,所以乘以4.
			{
        while(USART_GetFlagStatus(USART3,USART_FLAG_TC)==RESET);	//循环发送,直到发送完毕  		
				USART_SendData(USART3,p[i]); 

			} 
			if(KEY_Scan(0))	//有按键按下,需要处理
			{  
				//LCD_ShowString(30,210,210,16,16,"Quit Sending data   ");//提示退出数据传输
					printf("Quit Sending data\r\n ");
					effect++;
					if(effect>6)effect=0;
					OV2640_Special_Effects(effect);//设置特效
					sprintf((char*)msgbuf,"%s",EFFECTS_TBL[effect]);
					printf("--------------------\r\n         effect:%s\r\n --------------------\r\n",EFFECTS_TBL[effect]);
		
			//LCD_Fill(30,180,239,190+16,WHITE);
			//LCD_ShowString(30,180,210,16,16,msgbuf);//显示提示内容
				delay_ms(300); 				  
			}//else printf("Send data complete!!\r\n ");//提示传输结束设置 
			jpeg_data_ok=2;	//标记jpeg数据处理完了,可以让DMA去采集下一帧了.
		}		
	}    
} 

int main(void)
{ 

	NVIC_PriorityGroupConfig(NVIC_PriorityGroup_2);//设置系统中断优先级分组2
	delay_init(168);  //初始化延时函数
	uart_init(115200);		//初始化串口波特率为115200
	usart2_init(42,115200);		//初始化串口2波特率为115200
	usart3_init(460800);
	uart4_init(115200);
	LED_Init();					//初始化LED 
 
 	KEY_Init();					//按键初始化 
	TIM3_Int_Init(10000-1,8400-1);//10Khz计数,1秒钟中断一次
	
 	usmart_dev.init(84);		//初始化USMART
 
	while(OV2640_Init())//初始化OV2640
	{
		delay_ms(200);
		printf("OV2640 ERR\r\n");
		delay_ms(200);
	}
	printf("OV2640 OK\r\n");	  
 	while(1)
	{	
		jpeg_test();
	}


}

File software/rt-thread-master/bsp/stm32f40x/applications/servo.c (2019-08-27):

/*
 * servo.c
 *
 *  Created on: 2019年3月30日
 *      Author: zengwangfa
 *      Notes:  舵机设备
 */
#define  LOG_TAG    "servo"
#include <stdio.h>
#include <stdlib.h>
#include <rtthread.h>
#include <elog.h>

#include "sys.h"

#include "DataType.h"
#include "Control.h"
#include "ioDevices.h"
#include "servo.h"
#include "propeller.h"
#include "flash.h"
#include "ret_data.h"
#include "rc_data.h"
#include "focus.h"
#include "DeviceThread.h"

/*---------------------- Constant / Macro Definitions -----------------------*/

#define RoboticArm_MedValue  1500
#define YunTai_MedValue  		 2000

/*----------------------- Variable Declarations -----------------------------*/

ServoType RoboticArm = {
		 .MaxValue = 2000, 		//机械臂 正向最大值
		 .MinValue = 1000,	  //机械臂 反向
		 .MedValue = 1500,
	   .Speed  = 5//机械臂当前值
};  //机械臂
ServoType  YunTai = {
		 .MaxValue = 2500, 		//机械臂 正向最大值
		 .MinValue = 1500,	  //机械臂 反向
		 .MedValue = 2000,
	   .Speed  = 10//云台转动速度
};      //云台

uint16 propeller_power = 1500;
short _test_value = 0;


/*----------------------- Function Implement --------------------------------*/


/*******************************************
* 函 数 名：Servo_Output_Limit
* 功    能：舵机输出限制
* 输入参数：输入值：舵机结构体地址 
* 返 回 值：None
* 注    意：
********************************************/
void Servo_Output_Limit(ServoType *Servo)
{
		Servo->CurrentValue = Servo->CurrentValue > Servo->MaxValue ? Servo->MaxValue : Servo->CurrentValue ;//正向限幅
		Servo->CurrentValue = Servo->CurrentValue < Servo->MinValue ? Servo->MinValue : Servo->CurrentValue ;//反向限幅
	
}


/**
  * @brief  RoboticArm_Control(机械臂控制)
  * @param  控制指令 0x00：不动作  0x01：张开  0x02：关闭
  * @retval None
  * @notice 
  */
void RoboticArm_Control(uint8 *action)
{
		static uint8 on_off = 0;//自锁开关
		if(0 == on_off){
				on_off = 1;
				RoboticArm.CurrentValue = RoboticArm.MedValue;
		}
	
		switch(*action)
		{
				case 0x01:RoboticArm.CurrentValue += RoboticArm.Speed;
									if(RoboticArm.CurrentValue >= RoboticArm.MaxValue){device_hint_flag |= 0x01;}//机械臂到头标志
									else {device_hint_flag &= 0xFE;}; //清除机械臂到头标志

									break;
				case 0x02:RoboticArm.CurrentValue -= RoboticArm.Speed;
									if(RoboticArm.CurrentValue <= RoboticArm.MinValue){device_hint_flag |= 0x01;}//机械臂到头标志
									else {device_hint_flag &= 0xFE;}; //清除机械臂到头标志

									break;
				default:break;
		}
		Servo_Output_Limit(&RoboticArm);//机械臂舵机限幅
		TIM4_PWM_CH3_D14(RoboticArm.CurrentValue);
		*action = 0x00; //清除控制字
}




/**
  * @brief  YunTai_Control(云台控制)
  * @param  控制指令 0x00：不动作  0x01：向上  0x02：向下
  * @retval None
  * @notice 
  */

void YunTai_Control(uint8 *action)
{
		static uint8 on_off = 0;//自锁开关
		if(0 == on_off){
				on_off = 1;
				YunTai.CurrentValue = YunTai.MedValue;
		}
		switch(*action)
		{
				case 0x01:YunTai.CurrentValue -= YunTai.Speed;  //向上
						if(YunTai.CurrentValue <= YunTai.MaxValue){device_hint_flag |= 0x02;}//云台到头标志
						else {device_hint_flag &= 0xFD;}; //清除云台到头标志
						break;  
						
				case 0x02:YunTai.CurrentValue += YunTai.Speed; //向下
						if(YunTai.CurrentValue >= YunTai.MinValue){device_hint_flag |= 0x02;}//云台到头标志
						else {device_hint_flag &= 0xFD;}; //清除云台到头标志
						break;  

				case 0x03:YunTai.CurrentValue = YunTai.MedValue;
						break;   //归中
						
				default: 
						break;
		}
		Servo_Output_Limit(&YunTai);
		TIM4_PWM_CH4_D15(YunTai.CurrentValue); 
		*action = 0x00; //清除控制字
}








/*【吸取器】 修改 【测试】 MSH方法 */
static int xiquqi_value_set(int argc, char **argv)
{
    int result = 0;
    if (argc != 2){
        log_e("Error! Proper Usage: robotic_arm_currentValue_set <0~3000>");
				result = -RT_ERROR;
        goto _exit;
    }

		if(atoi(argv[1]) <= 3000 ){		
				_test_value = atoi(argv[1]);
				log_i(" Value:  %d",_test_value);
				TIM3_PWM_CH3_B0(_test_value);
		}
		else {
				log_e("Error! The value is out of range!");
		}
_exit:
    return result;
}
MSH_CMD_EXPORT(xiquqi_value_set,ag: xiquqi_value_set <0~3000>);





/*【云台】舵机 修改 【当前】 MSH方法 */
static int robotic_arm_currentValue_set(int argc, char **argv)
{
    int result = 0;
    if (argc != 2){
        log_e("Error! Proper Usage: robotic_arm_currentValue_set <0~3000>");
				result = -RT_ERROR;
        goto _exit;
    }

		if(atoi(argv[1]) <= 3000 ){		
				RoboticArm.CurrentValue = atoi(argv[1]);
				log_i(" Value:  %d",RoboticArm.CurrentValue);
				TIM4_PWM_CH3_D14(RoboticArm.CurrentValue);


		}
		else {
				log_e("Error! The value is out of range!");
		}
_exit:
    return result;
}
MSH_CMD_EXPORT(robotic_arm_currentValue_set,ag: robotic_arm_currentValue_set <0~3000>);





/*【机械臂】舵机 修改 速度值 */
static int robotic_arm_speed_set(int argc, char **argv)
{
    int result = 0;
    if (argc != 2){
        log_e("Error! Proper Usage: RoboticArm_Speed 10");
				result = -RT_ERROR;
        goto _exit;
    }
		if(atoi(argv[1]) <= 255 && atoi(argv[1]) > 0){
				RoboticArm.Speed = atoi(argv[1]);
				Flash_Update();
				log_i("Write_Successed! RoboticArm.Speed:  %d",RoboticArm.Speed);
		}
		
		else {
				log_e("Error! The value is out of range!");
		}
_exit:
    return result;
}
MSH_CMD_EXPORT(robotic_arm_speed_set,ag: robotic_arm_speed_set 10);


/*【机械臂】舵机 修改 【正向最大值】MSH方法 */
static int robotic_arm_maxValue_set(int argc, char **argv)
{
    int result = 0;
    if (argc != 2){
        log_e("Error! Proper Usage: RoboticArm_Maxvalue_set 1600");
				result = -RT_ERROR;
        goto _exit;
    }
		if(atoi(argv[1]) <= 5000 && atoi(argv[1]) >= 1500){
				RoboticArm.MaxValue = atoi(argv[1]);
				Flash_Update();
				log_i("Write_Successed!  RoboticArm.MaxValue:  %d",RoboticArm.MaxValue);
		}
		
		else {
				log_e("Error! The value is out of range!");
		}
_exit:
    return result;
}
MSH_CMD_EXPORT(robotic_arm_maxValue_set,ag: robotic_arm_openvalue_set 2000);




/*【机械臂】舵机 修改 【反向最大值】 MSH方法 */
static int robotic_arm_minValue_set(int argc, char **argv)
{
    int result = 0;
    if (argc != 2){
        log_e("Error! Proper Usage: RoboticArm_minvalue_set 1150");
				result = -RT_ERROR;
        goto _exit;
    }
		if(atoi(argv[1]) <= 3000 &&  atoi(argv[1]) >= 500){
				RoboticArm.MinValue = atoi(argv[1]);
				Flash_Update();
				log_i("Write_Successed!  RoboticArm.MinValue:  %d",RoboticArm.MinValue);
		}
		else {
				log_e("Error! The value is out of range!");
		}

		
		
_exit:
    return result;
}
MSH_CMD_EXPORT(robotic_arm_minValue_set,ag: robotic_arm_closevalue_set 1500);


/*【机械臂】舵机 修改 速度值 */
static int yuntai_speed_set(int argc, char **argv)
{
    int result = 0;
    if (argc != 2){
        log_e("Error! Proper Usage: yuntai_speed_set 5");
				result = -RT_ERROR;
        goto _exit;
    }
		if(atoi(argv[1]) <= 255 && atoi(argv[1]) > 0){
				YunTai.Speed = atoi(argv[1]);
				Flash_Update();
				log_i("Write_Successed! YunTai.Speed:  %d",YunTai.Speed);
		}
		else {
				log_e("Error! The value is out of range!");
		}
_exit:
    return result;
}
MSH_CMD_EXPORT(yuntai_speed_set,ag: yuntai_speed_set 5);
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

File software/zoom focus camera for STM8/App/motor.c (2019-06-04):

#include "bsp_timer.h"
#include "motor.h"
#include "bsp_timer.h"

//unsigned char F_Rotation[8]={0x08,0x0c,0x04,0x06,0x02,0x03,0x01,0x09} ;  //单双8拍反转表 五线四相步进电机表
//unsigned char R_Rotation[8]={0x09,0x01,0x03,0x02,0x06,0x04,0x0c,0x08} ;  //单双8拍正转表

unsigned char F_Rotation[4]={0x09,0x0A,0x06,0x05} ;  //4拍正转表  Forward
unsigned char R_Rotation[4]={0x05,0x06,0x0A,0x09} ;  //4拍反转表  Reverse


/******************************************************************************
* Name: 	 STEP_Init
*
* Desc: 	 初始化两个两相四线步进电机引脚
* Param:   无
* Return:  无
* Note:    本函数为 变焦、聚焦控制的步进电机引脚初始化
* Author:  Dwfish
* -------------------------------------
* Log: 	 2018/12/27, Create this function by Dwfish
 ******************************************************************************/
void STEP_Init()
{
     CLK_HSIPrescalerConfig(CLK_PRESCALER_HSIDIV1); //HSI = 16M (1分频)  //时钟配置
     
     GPIO_Init(GPIOD, (GPIO_Pin_TypeDef)ZOOM_A1, GPIO_MODE_OUT_PP_LOW_FAST); //初始化两个两相四线步进电机引脚
     GPIO_Init(GPIOD, (GPIO_Pin_TypeDef)ZOOM_A0, GPIO_MODE_OUT_PP_LOW_FAST);
     GPIO_Init(GPIOA, (GPIO_Pin_TypeDef)ZOOM_B1, GPIO_MODE_OUT_PP_LOW_FAST);
     GPIO_Init(GPIOC, (GPIO_Pin_TypeDef)ZOOM_B0, GPIO_MODE_OUT_PP_LOW_FAST);
     
     GPIO_Init(FOCUS_STEP_PORT, (GPIO_Pin_TypeDef)FOCUS_A1, GPIO_MODE_OUT_PP_LOW_FAST);
     GPIO_Init(FOCUS_STEP_PORT, (GPIO_Pin_TypeDef)FOCUS_A0, GPIO_MODE_OUT_PP_LOW_FAST);
     GPIO_Init(FOCUS_STEP_PORT, (GPIO_Pin_TypeDef)FOCUS_B1, GPIO_MODE_OUT_PP_LOW_FAST);
     GPIO_Init(FOCUS_STEP_PORT, (GPIO_Pin_TypeDef)FOCUS_B0, GPIO_MODE_OUT_PP_LOW_FAST);
     
     GPIO_Init(GPIOD, (GPIO_Pin_TypeDef)GPIO_PIN_4, GPIO_MODE_OUT_PP_LOW_FAST); //LED
     
     GPIO_WriteLow(GPIOD,ZOOM_A1);   //输出低
     GPIO_WriteLow(GPIOD,ZOOM_A0);
     GPIO_WriteLow(GPIOA,ZOOM_B1);
     GPIO_WriteLow(GPIOC,ZOOM_B0);
     
     GPIO_WriteLow(FOCUS_STEP_PORT,FOCUS_A1);
     GPIO_WriteLow(FOCUS_STEP_PORT,FOCUS_A0);
     GPIO_WriteLow(FOCUS_STEP_PORT,FOCUS_B1);
     GPIO_WriteLow(FOCUS_STEP_PORT,FOCUS_B0);
     
     GPIO_WriteLow(GPIOD,GPIO_PIN_4);
     
}


void STEP_Stop(void)
{
     GPIO_WriteLow(GPIOD,ZOOM_A1);   //输出低
     GPIO_WriteLow(GPIOD,ZOOM_A0);
     GPIO_WriteLow(GPIOA,ZOOM_B1);
     GPIO_WriteLow(GPIOC,ZOOM_B0);
     
     GPIO_WriteLow(FOCUS_STEP_PORT,FOCUS_A1);
     GPIO_WriteLow(FOCUS_STEP_PORT,FOCUS_A0);
     GPIO_WriteLow(FOCUS_STEP_PORT,FOCUS_B1);
     GPIO_WriteLow(FOCUS_STEP_PORT,FOCUS_B0);
}

/******************************************************************************
* Name: 	 SetMotor
*
* Desc: 	 使步进电机转动
* Param:   电机编号:Motor_ID[0为变焦、1为聚焦]     传入:InputData选择相位使能
* Return:  无
* Note:    根据自己定义的节拍表输出相应脉冲
* Author:  Dwfish
* -------------------------------------
* Log: 	 2018/12/27, Create this function by Dwfish
 ******************************************************************************/
void SetMotor(unsigned char Motor_ID,unsigned char InputData)    //根据传送的数据Inputdata设置PB12-PB15引脚输出
{
    if(InputData & 0x08){
				switch(Motor_ID){
					case ZOOM_MOTOR : GPIO_WriteHigh(GPIOD, ZOOM_A1 );	break;
					case FOCUS_MOTOR : GPIO_WriteHigh(FOCUS_STEP_PORT, FOCUS_A1 );break;
				}					
    }
    else {
		  	switch(Motor_ID){
					case ZOOM_MOTOR : GPIO_WriteLow(GPIOD, ZOOM_A1 );	break;
					case FOCUS_MOTOR : GPIO_WriteLow(FOCUS_STEP_PORT, FOCUS_A1 );break;
				}	
    }
	 
    if(InputData & 0x04){
				switch(Motor_ID){
					case ZOOM_MOTOR : GPIO_WriteHigh(GPIOD, ZOOM_A0 );	break;
					case FOCUS_MOTOR : GPIO_WriteHigh(FOCUS_STEP_PORT, FOCUS_A0 );break;
				}	  
    }
   else{
		  	switch(Motor_ID){
					case ZOOM_MOTOR : GPIO_WriteLow(GPIOD, ZOOM_A0 );	break;
					case FOCUS_MOTOR : GPIO_WriteLow(FOCUS_STEP_PORT, FOCUS_A0 );break;
				}	
    }
		
    if(InputData & 0x02){
				switch(Motor_ID){
					case ZOOM_MOTOR : GPIO_WriteHigh(GPIOA, ZOOM_B1 );	break;
					case FOCUS_MOTOR : GPIO_WriteHigh(FOCUS_STEP_PORT, FOCUS_B1 );break;
				}	   
    }
    else{
		  	switch(Motor_ID){
					case ZOOM_MOTOR : GPIO_WriteLow(GPIOA, ZOOM_B1 );	break;
					case FOCUS_MOTOR : GPIO_WriteLow(FOCUS_STEP_PORT, FOCUS_B1 );break;
				}	
    }
    if(InputData & 0x01){
				switch(Motor_ID){
					case ZOOM_MOTOR : GPIO_WriteHigh(GPIOC, ZOOM_B0 );	break;
					case FOCUS_MOTOR : GPIO_WriteHigh(FOCUS_STEP_PORT, FOCUS_B0 );break;
				}	  
    }
    else{
				switch(Motor_ID){
					case ZOOM_MOTOR : GPIO_WriteLow(GPIOC, ZOOM_B0 );	break;
					case FOCUS_MOTOR : GPIO_WriteLow(FOCUS_STEP_PORT, FOCUS_B0 );break;
				}	
    }
}

/******************************************************************************
* Name: 	 MotorNCircle
*
* Desc: 	 电机转动 N 圈
* Param:   电机编号:Motor_ID     转动n圈     正反：position【0正1反】
* Return:  无
* Note:    无
* Author:  Dwfish
* -------------------------------------
* Log: 	 2018/12/27, Create this function by Dwfish
 ******************************************************************************/
void MotorNCircle(unsigned char Motor_ID,int n,bool position)
{
   int i=0;
   int j=0;
   int k=0;
   for(j=0;j<n;j++)
   {
      for(i=0;i<4*128;i++)   //极限是4*128
		 {
          for(k=0;k<4;k++)
				 {
              if(TRUE == position)
                 SetMotor(Motor_ID,R_Rotation[k]);  //1反转
             else
                 SetMotor(Motor_ID,F_Rotation[k]);    
                TIMDelay_N10us(100);
          }
      }
    }
}

/******************************************************************************
* Name: 	 MotorNAngle
*
* Desc: 	 电机转动 N °
* Param:   电机编号:Motor_ID     转动n°     正反：position【0正1反】
* Return:  无
* Note:    第二个for循环中i所对应的i<1中"1"参数，需要根据自己实际步进电机调整
* Author:  Dwfish
* -------------------------------------
* Log: 	 2018/12/27, Create this function by Dwfish
 ******************************************************************************/

void MotorNAngle(unsigned char Motor_ID,int n,bool position) //n为步进电机转动的角度为n*120，position为正转或者反转
{
   int i=0;
   int j=0;
   int k=0;
   for(j=0;j<n;j++)
   {
      for(i=0;i<1;i++)     
      {
          for(k=0;k<4;k++)   
          {
              if(TRUE == position)
                 SetMotor(Motor_ID,R_Rotation[k]);  
              else
                 SetMotor(Motor_ID,F_Rotation[k]);  
             	TIMDelay_N10us(100);      
          }
      }
    }
}

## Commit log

2019-01-17 提交hardware【未完成】
    [ROBOT.PrjPcb, Underwater_vehicle.PcbDoc, Underwater_vehicle.SchDoc]
2019-01-20 更新 1.20 22:43
    [ROBOT.PrjPcb, Underwater_vehicle.PcbDoc, Underwater_vehicle.SchDoc]
2019-01-21 已完成V1.00
    [Underwater_vehicle.SchDoc]
2019-01-22 更新PCB细节
    [ROBOT.PrjPcb, Underwater_vehicle.SchDoc]
2019-01-26 提交摄像头测试程序v1.00
2019-01-26 提交相关参考文档
    [JMU 2018 Camera主板 2.0 核心板.16_1第二板.SchDoc]
2019-02-07 提交相关驱动代码 LED/KEY
    [kconfig-language.txt, kconfig.txt]
2019-02-07 一些修改
2019-02-09 Creat OLED Thread.
2019-02-09 添加get等方法
2019-02-12 更新相关MSH方法
2019-02-13 创建可更改舵机开启值/关闭值MSH 方法.
    [Underwater_vehicle.SchDoc]
2019-02-15 update 一些方法
    [ROBOT.PrjPcb, Underwater_vehicle.SchDoc]
2019-02-17 更新 README.md 添加相应完成项 与 未完成项，梳理整体框架 【为完成 相应外设表】
2019-02-17 update OLED电子罗盘 && 修复了一些bug.
    [key.c, main.c]
2019-02-17 删除目录software/rt-thread-master/bsp/stm32f20x
2019-02-17 删除目录software/rt-thread-master/bsp/stm32f10x
2019-02-17 删除目录software/rt-thread-master/bsp/stm32f10x-HAL
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2019-02-18 提交相关软硬件及文档
    [mos双驱.SchDoc, 会车驱动.PcbDoc, 会车驱动_by_cjx.PrjPCB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]
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2019-02-18 修复一些bug
2019-02-21 update 2.0 (远程下载/ Camera接口改正/ 增加wifi连接IO
    [Underwater_vehicle.SchDoc]
2019-02-22 增加wifi连接检测/Camera接口改正/BOOT0..
    [Underwater_vehicle.SchDoc]
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2019-02-25 添加了一下msh方法 与 一种 log方法
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2019-02-28 【更新】添加easylog && easyflash && update msh
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2019-03-03 【更新】添加Camera && 修复了一些bug
2019-03-04 【更新】修复了一些bug.
2019-03-07 【更新】
    [ANO_XIEYI.xlsx, JMU 2018 Camera主板 2.0 核心板.16_1第二板.SchDoc, ROBOT.PrjPcb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]
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2019-03-12 【更新】修复匿名地面站读写FLASH问题
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2019-03-23 【更新】修复了一些bug
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2019-03-25 【更新】更新板子相关接口
    [Underwater_vehicle-V3.0.SchDoc]
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2019-03-26 【更新】提交变焦摄像头驱动电路
    [ROBOT.PrjPcb, Underwater_vehicle-V3.0.SchDoc, ZOOM_Camera_drive.PrjPcb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]
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2019-03-31 【更新】修复了MS5837传感器采集出错问题
2019-04-03 【更新】修复了头文件重复包含的问题
2019-04-08 【更新】完善原理图
    [Underwater_vehicle-V3.0.SchDoc]
2019-04-18 【更新】修复了相关程序结构
2019-04-18 【更新】提交主板PCB
    [ROV_MainBoard V2.0.SchDoc, ROV_Mainboard.PrjPcb, ROV_Power V2.0.SchDoc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]
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2019-04-20 【更新】添加返回数据协议以及修复了一些bug
2019-04-23 【更新】修复了update方法
2019-04-24 【更新】修复了不能debug发送的问题
2019-04-25 【更新】变焦摄像头底板V2.0
    [ZOOM_Camera_drive.PrjPcb, Zoom_Camera.SchDoc]
2019-05-07 【更新】提交相关文档
    [ROV_Power V2.0.SchDoc, Underwater_vehicle-V3.0.SchDoc]
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2019-05-13 【更新】修复了间断性控制问题
2019-05-13 【更新】提交树莓派相关设计文档
    [Raspberry-Pi-B-Plus-V1.2-Mechanical.dxf]
2019-05-13 【更新】提交变焦摄像头控制板
    [STM8.SchDoc, stm8.PrjPcb, 变焦摄像头v2.0.PcbDoc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]
2019-05-14 【更新】解决了变焦摄像头通信异常问题
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2019-05-16 【更新】修正指南针数值
2019-05-18 【更新】提交电源仓主板V1.0
    [PowerBoard.PcbDoc, PowerBoard.SchDoc]
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2019-06-13 【完善】修复了一些bug,还存在推进器会异常打开，以及复位 电机反转问题
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2019-06-24 【替换】完善目录结构
    [ROBOT.PrjPcb, ROV_MainBoard V2.0.SchDoc, ROV_Mainboard.PrjPcb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]
2019-06-24 【提交】更新核心板V3.0,稳压源换为TPS7333
    [ROBOT.PrjPcb, Underwater_vehicle-V3.0.SchDoc]
2019-06-24 【更新】修改完善Core Board丝印说明
    [ROBOT.PrjPcb, Underwater_vehicle-V3.0.SchDoc]
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2019-06-26 【替换】核心控制板名字修改为Core Controller V3.0
    [Core Controller V3.0.PrjPcb, Core Controller V3.0.SchDoc, Underwater_vehicle-V3.0.SchDoc]
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2019-06-30 修改变焦摄像头pcb板及原理图
    [Zoom Camrea Controller V3.0.PrjPcb, Zoom Camrea Controller V3.0.SchDoc]
2019-06-30 【更新】完善控制器结构体,新增总开关,修复了数据包一直正确的bug
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2019-06-30 【更新】修复变焦摄像头控制板一些bug
    [Underwater_vehicle-V2.0.PrjPcb]
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2019-06-30 【更新】修复说明文档中的显示异常
2019-06-30 【更新】修复了LED状态bug，完善数据收发函数控制
2019-07-02 【更新】提交机器人主板V3.0(改善接口及电源设计)
    [ROV_MainBoard V2.0.SchDoc, ROV_Mainboard.PrjPcb, ROV_Power V2.0.SchDoc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]
2019-07-03 【更新】更新机器人主板V3.0,完善丝印层设置
    [Robot-Control V3.0.SchDoc, Robot-Power V3.0.SchDoc, Robot设备对应表.xlsx]
2019-07-03 【更新】更新机器人主板 V3.0
    [Robot-Control V3.0.SchDoc, Robot-Power V3.0.SchDoc]
2019-07-03 【更新】提交 Vicor V300A24T500 DataSheet
2019-07-04 【修复】修复了一些bug:MS5837精度值、控制结构; 【添加】添加获取摇杆 矢量值
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2019-07-06 【提交】提交深度传感器MS5837 V1.0
    [MS5837 V1.0.PcbDoc, MS5837 V1.0.PrjPCB, MS5837 V1.0.SchDoc]
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2019-07-09 【更新】提交电源控制器 电路&PCB&控制盒 设计
    [Power Controller V1.0.PcbDoc, Power Controller V1.0.PrjPcb, Power Controller V1.0.SchDoc]
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2019-07-09 【修复】修复主板丝印层对应错误
2019-07-12 【更新】更新核心板4.0(新增 蓝牙接口、去除JMU LOGO)
    [Core Controller V4.0.PrjPcb, Core Controller V4.0.SchDoc]
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2019-07-12 【更新】提交 舱内 电源控制板V1.0
    [Power Controller In ROV V1.0.PcbDoc, Power Controller In ROV V1.0.PrjPcb, Power Controller In ROV V1.0.SchDoc]
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2019-07-13 【修复】修改了 PLC模块禁止布线GND，防止GND的干扰
    [Power Controller In ROV V1.0.PcbDoc]
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2019-07-13 【更新】修复了 期望深度值 超出范围
2019-07-14 【更新】修复了 深度传感器 漂移问题
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2019-07-14 【修复】添加 左摇杆优先级大于 右摇杆（自旋）设定
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2019-07-18 【更新】提交电源控制板 V2.0
    [Power Controller V2.0.PcbDoc, Power Controller V2.0.PrjPcb, Power Controller V2.0.SchDoc]
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2019-07-20 【更新】优化程序
    [MS5837 V1.0.PcbDoc, MS5837 V1.0.PrjPCB, MS5837 V1.0.SchDoc]
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2019-07-20 【更新】 1.改进推进器速度补偿。 2.优化OLED电源图标。 3.增加推进器调控机制。
2019-07-21 【提交】提交SPL1301 歌尔(改)深度传感器
    [Depth Sensor for SPL1301 V1.0.PcbDoc, Depth Sensor for SPL1301 V1.0.PrjPCB, Depth Sensor for SPL1301 V1.0.SchDoc]
2019-07-21 【更新】删除rtt文件夹
    [kconfig-language.txt, kconfig.txt]
2019-07-21 【更新】 1.优化速度补偿函数 2.优化OLED电源显示 3.增加推进器调试参数
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2019-07-23 【更新】修复了 指南针 补偿偏角问题
2019-07-23 【更新】 1.增加四轴水下机器人推进器控制算法。 2.增加按键调试模式。 3.增加模式切换。 【发现问题】 云台按键未能执行相应程序，会重复上一指令。
    [sensor.c, servo.c]
2019-07-23 【更新】修复了OLED显示bugs，完善Flash参数自检 isnan
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2019-07-25 【bugs】修复了PWM3初始化 失败问题
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2019-07-28 【重要】添加四浆ROV核心运动公式，修复了推进器瞬间反转问题
2019-07-29 【提交】提交相关设计文档
    [摇杆数据跳变测试.xlsx]
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2019-07-30 【更新】修复了推进器PWM 瞬间突变bugs
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2019-07-31 【更新】加大INA169分压电阻，以防ADC采集数据异常
    [Robot-Power V3.0.SchDoc]
2019-07-31 【更新】添加自带解算的深度传感器MS5837
    [MS5837 V2.0.PcbDoc, MS5837 V2.0.SchDoc, STM32 for MS5837 V1.0.PcbDoc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]
2019-07-31 【更新】提交USB转UART自带串口
    [USB to UART With Zigbee V1.0.PcbDoc, USB to UART With Zigbee V1.0.PrjPcb, USB to UART With Zigbee V1.0.SchDoc]
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2019-07-31 【更新】修复了电流采集异常问题
2019-08-01 【更新】提交 机器人主板V4.0，添加防倒灌 大功率二极管
    [Robot-Control V4.0.SchDoc, Robot-MainBoard V4.0.PrjPcb, Robot-Power V4.0.SchDoc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]
2019-08-03 【更新】提交 机器人主板V4.0，添加防倒灌 二极管
    [Robot-Control V4.0.SchDoc, Robot-MainBoard V4.0.PrjPcb, Robot-Power V4.0.SchDoc]
2019-08-22 【修复】修复了无法使能脚本的问题
2019-08-23 【更新】提交探照灯 原理图PCB设计
    [Search Light V1.0.SchDoc]
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2019-08-25 【更新】修复bugs
2019-08-26 【修复】修复了云台初始化不归中问题
2019-10-11 【更新】修复居中问题
2019-10-14 【更新】完善目录结构
    [SPL1301 for Cal V1.0.PcbDoc, SPL1301 for Cal V1.0.SchDoc, STM32 for Cal V1.0.PcbDoc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]
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2019-10-14 【更新】完善并修复python服务器经常无法启动的原因
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2020-01-03 【更新】:book:完善
    [MS5837 V1.0.PrjPCB, Power Controller In ROV V1.0.PrjPcb, Power Controller In ROV V1.0.SchDoc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]
2020-05-17 :hammer: modify: 修复原理图电源指示灯电压错误
    [Zoom Camrea Controller V3.0.PcbDoc, Zoom Camrea Controller V3.0.SchDoc]
2020-05-17 :memo: Add: 添加配件图片
    [Core Controller V4.0.SchDoc, ROV_Power V2.0.SchDoc]
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2020-05-22 :sparkles: Add: 添加klm matlab仿真

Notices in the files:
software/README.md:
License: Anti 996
